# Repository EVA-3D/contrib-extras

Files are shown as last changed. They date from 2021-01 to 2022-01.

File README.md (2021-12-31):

# EVA-3D community contributions
This is the place that houses the community contributions that do not necessarily conform 100% to the standard EVA defines, but may still be useful in specific applications. This is also a place to share other things like spool holders, test prints, etc. If you have a part or a mod you want to list here, fork this repository, add your files, and [submit a pull request](https://github.com/EVA-3D/contrib-extras/pulls). Anyone is welcome to contribute, in fact, the more the merrier!

# How to contribute
Fork this repository and add your stls, an image preview and a page file for presenting your part.

Part descriptions are written in markdown (.md) files.

* The main page for your part should be in `docs/[category]/[your_part_name].md`
* Any assets linked from that page (images, etc) should be in `docs/[category]/assets`. All files should be prefixed with your part name.
* The STL(s) should be in `docs/[category]/stl`. All files should be prefixed with your part name.
* Take a look at [Pawel's Spool Holder](https://github.com/EVA-3D/contrib-extras/tree/main/docs/spool_holders) for inspiration.

If you're not familiar with Git, reach out to `@miklschmidt#2036` on discord, or get help on [the unofficial Rat Rig discord server](https://discord.gg/D62e8XNeYa).

Please note that all contributes are automatically subject to the terms of the [CC BY-SA 4.0 license](https://creativecommons.org/licenses/by-sa/4.0/).

Please! Share your candy!

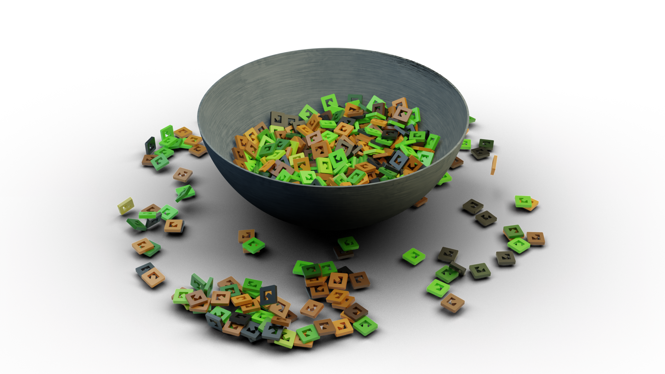
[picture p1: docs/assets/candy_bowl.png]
candy


## Local deployment 

There are two options, either you have a local Python envorinment with `Python` and `Poetry` or you can use Docker - the latter is easier but will be troublesome on Windows (since Windows is troublesome).

To get Docker go to https://docs.docker.com/get-docker/ and proceed with the installation steps. Do not be affraid in case you see this as black magic, Docker is a tool that allowes to run a tiny version of a Linux system on Mac, Windows and Linux - that tindy system is isolated from your machine - it's like a sandbox for developers.

> Per the documentation:
> It remains free for small businesses (fewer than 250 employees AND less than $10 million in annual revenue), **personal use**, education, and **non-commercial open source projects**.

Once it's installed you can use Docker Compose to deploy your own private EVA contrib site that will be visible only to you, go ahead and experiment with it to make sure your changes work before making a pull request :)

```
docker-compose up
```

And your local site will be accessible on the 127.0.0.1 address with is the loopback address pointing to your own machine: http://127.0.0.1:62999 is the full address and port.

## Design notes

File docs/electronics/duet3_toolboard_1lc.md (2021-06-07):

---
title: WichuR's Toolboard 1LC Horizontal Mount
---

> Created by: [Maciej Raczyński](https://github.com/wichur)

Allows mounting a Duet Toolboard 1LC v1.1 to the back plate in horizontal position. Alligned to keep within side boundaries of duct horns.

## Features
 - Positioned horizontally, above print fan
 - Vertical post for cable strain relief
 - Zip tie holes (2.5mm) for cable management
 - Place to support PTFE tube that helps to guide cables

## Compatibility
 - EVA 2.2.0 
 - Duet Toolboard 1LC v1.1
 - duet3_toolboard_1lc_common_support *Should* work also for v1.0

## Related EVA Parts
 - Replaces cable fin

## Assembly
 - Attaching Driver0 and IO connectors requires to temporarily unscrew toolboard
 - Use shorter screws to attach board to support
 - Use longer screws to attach lid

| No | Qty | Name | Printable |
| -- | --- | --- | --- |
| 1  | 2 | M3 x 8 mm | No |
| 2  | 2 | M3 x 18 mm | No |
| 3  | 4 | M3 Hex nuts | No |
| 3  | 10  | >2.5mm zip ties (optional) | No |
| 8  | 1 | Common Board Support | [Yes](stl/duet3_toolboard_1lc_common_support.stl) |
| 9  | 1 | Lid for Toolboard 1LC v 1.1(optional) | [Yes](stl/duet3_toolboard_1lc_v11_lid.stl) |

### How to attach incoming cables (CAN, VIN, PTFE tube, nylon sleeve)
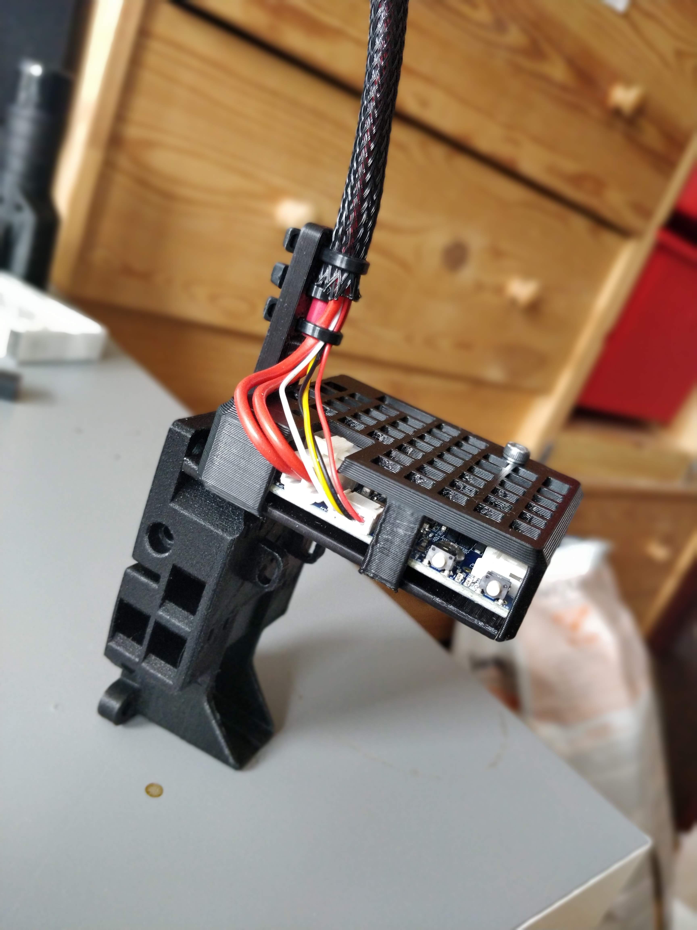
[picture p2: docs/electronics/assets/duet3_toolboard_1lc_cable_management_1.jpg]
cable management 1


### Sample cable management from appliances
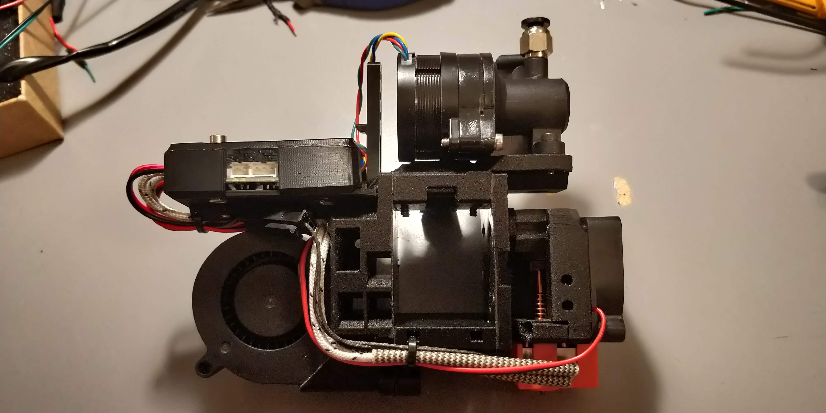
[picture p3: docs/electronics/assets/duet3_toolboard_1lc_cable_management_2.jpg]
cable management 2

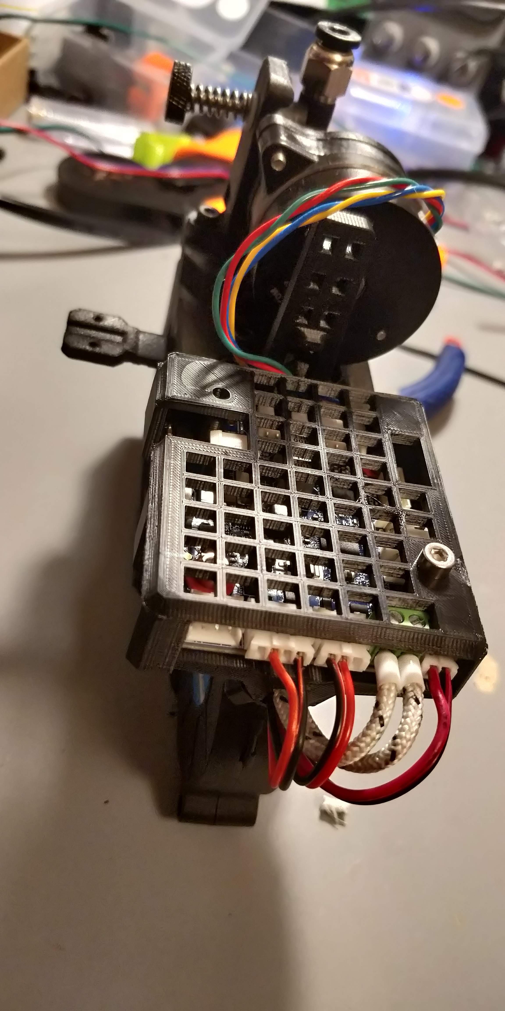
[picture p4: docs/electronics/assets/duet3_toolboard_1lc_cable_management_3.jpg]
cable management 3


### Print orientation
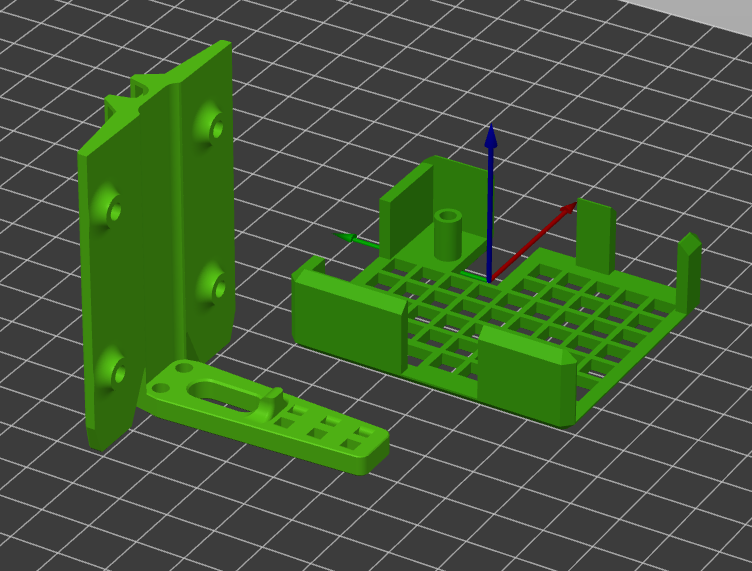
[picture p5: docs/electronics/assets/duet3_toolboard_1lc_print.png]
toolboard 1LC print orientation


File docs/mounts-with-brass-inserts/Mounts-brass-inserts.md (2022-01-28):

---
title: top_gun_de's Brass Inserts Remix
---

## Description:
> Created by: [Detlev Rackow](https://github.com/top-gun)

EVA is designed as a beginner-friendly carriage system, it is based on M3-screws and regular hex nuts. Brass inserts have several advantages over hex nuts: They won't fall out, and the risk of damage from too much torque is lower, especially in ABS and ASA parts. Inserting a brass inserts requires a soldering iron, and the inserts are a bit more expensive than the nuts.

EVA 2.4.1 was just released, and I modified relevant parts to accept brass inserts. The recommended sizes are M3x4.6x4 and M3x5x4. Don't use M3x5.6x4, as some holes are close to edges.

This repository contains 19 parts from EVA and two parts from the 5015 dual fan mod from Supersniffles.

I recommend to use these parts and complete your build with the parts from the regular EVA repository. The bottom part, for example, has no nut pockets so I did not modify it. The same is true for the probe mounts. You get these from the regular EVA 2.4-repository on github.

The "core" of EVA consists of:
- Universal face: Use from this contrib. Don't use the regular one, or support parts will get you into trouble.
- Top plate (holds the extruder): For Orbiter and Sherpa, use this contrib. For others use the regular parts.
- Bottom plate: Use from this contrib.
- Back plate (core-xy or cartesian): Use from this contrib.

To that, you attach a hotend face, most of these need a support part, too. Don't mix brass-fitted faces with regular support parts, they won't fit.

Fan ducts: These depend on the backplate. I clustered them into the carriage parts, together with the back plates.

Probe mounts: Use the regular ones. They have no nut pockets.

Shrouds: Use the regular parts. No nut pockets either.

## Compatible EVA versions

EVA 2.4.0 or later

## Carriage
### BOM - Carriage

| No | Qty | Name | Printable | Source
| -- | --- | --- | --- | ---
| 1  | 1 | Universal plate-brass | [Yes](stl/universal_face-2.4.1-inserts.stl) | [Onshape](https://cad.onshape.com/documents/74778ed34247d7556e100400/w/a58d330b6eac41d3ee1d6257/e/2d71e9f03f608830dc147b9e)
| 2  | 1 | backplate Core XY | [Yes](stl/back_corexy-2.4.1-inserts.stl) |  [Onshape](https://cad.onshape.com/documents/74778ed34247d7556e100400/w/a58d330b6eac41d3ee1d6257/e/5f6109f91396259629d149cf)
| 2a | 1 | backplate Cartesian | [Yes](stl/back_cartesian-2.4.1-inserts.stl) |  [Onshape](https://cad.onshape.com/documents/94ffc61ea8de2e8b4d175cb5/w/45370a8d35a588c223676b4b/e/29da292ee8a01c0ce953947a)
| 2b | 1 | backplate CoreXY-dual 5015 Supersniffles | [Yes](stl/dual_5015_back_v3_heat_inserts.stl) |  [Onshape](https://cad.onshape.com/documents/79d9ad219cc5cc9ce0dcf704/w/b53269836ac593db847c52c7/e/6edbe9540efb021b6a6e376c)
| 3  | 1 | Bottom plate MGN12 | [Yes](stl/bottom_mgn12_short_duct-inserts.stl) |  [Onshape](https://cad.onshape.com/documents/74778ed34247d7556e100400/w/a58d330b6eac41d3ee1d6257/e/884e27c8b1dbb4fb2e92761c)
| 3a | 1 | Bottom plate Dual 5015 MGN12 Supersniffles | [Yes](stl/dual_5015_bottom_v3.stl) |  [Onshape](https://cad.onshape.com/documents/9c252f9471d1d23ee56d6b70/w/959fe6d1b6f12c8dfe326720/e/2e778d9372bc94c95344f2a8)
| 4  | 1 | Tri-horn fan duct default | [Yes](stl/TriHorn-Duct-Default-2.4.2-inserts.stl) |  [Onshape](https://cad.onshape.com/documents/0032726621935a272d71ecdd/w/8c7ff9e179be83096c43302e/e/2895bb5dddef3b905fc26f3c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)
| 4a | 1 | Tri-horn fan duct default narrow | [Yes](stl/TriHorn-Duct-Default-Narrow-2.4.2-inserts.stl) |  [Onshape](https://cad.onshape.com/documents/0032726621935a272d71ecdd/w/8c7ff9e179be83096c43302e/e/2895bb5dddef3b905fc26f3c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)
| 4b | 1 | Tri-horn fan duct high | [Yes](stl/TriHorn-Duct-High-2.4.2-inserts.stl) |  [Onshape](https://cad.onshape.com/documents/0032726621935a272d71ecdd/w/8c7ff9e179be83096c43302e/e/2895bb5dddef3b905fc26f3c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)
| 4c | 1 | Tri-horn fan duct high narrow | [Yes](stl/TriHorn-Duct-High-Narrow-2.4.2-inserts.stl) |  [Onshape](https://cad.onshape.com/documents/0032726621935a272d71ecdd/w/8c7ff9e179be83096c43302e/e/2895bb5dddef3b905fc26f3c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)
| 4d | 1 | Tri-horn fan duct Volcano/Rapido UHF | [Yes](stl/TriHorn-Volcano-Duct-UHF-2.4.2-inserts.stl) |  [Onshape](https://cad.onshape.com/documents/0032726621935a272d71ecdd/w/8c7ff9e179be83096c43302e/e/2895bb5dddef3b905fc26f3c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)
| 4e | 1 | Dual 5015 Monster horn duct Supersniffles | [Yes](stl/dual_5015_monster_horns_duct_v2.3_heat_inserts.stl) |  [Onshape](https://cad.onshape.com/documents/9c252f9471d1d23ee56d6b70/w/959fe6d1b6f12c8dfe326720/e/18901272a3158b3c621a46d2)
| 4f | 1 | Dual 5015 Volcano/Rapido UHF duct (Tobi) | [Yes](stl/horn-rapido-uhf-2.4.1-inserts.stl) |  [Onshape](https://cad.onshape.com/documents/d0c8871ffd12a03b94cb6b30/w/60becf0a1f7f2dc8485e1bea/e/336a4f443bbbc477c9fbf4a0)
| 5  | 1 | Universal cable mount | [Yes](stl/unversal_cable_mount-2.4.2-inserts.stl) | [Onshape](https://cad.onshape.com/documents/74778ed34247d7556e100400/w/a58d330b6eac41d3ee1d6257/e/74e3872d67a8b60bdf4ad503)
| 6  | ##  | heat inserts brass M3 x D4.6 x L4 | No | [AliExpress](https://aliexpress.com/item/4000232858343.html)

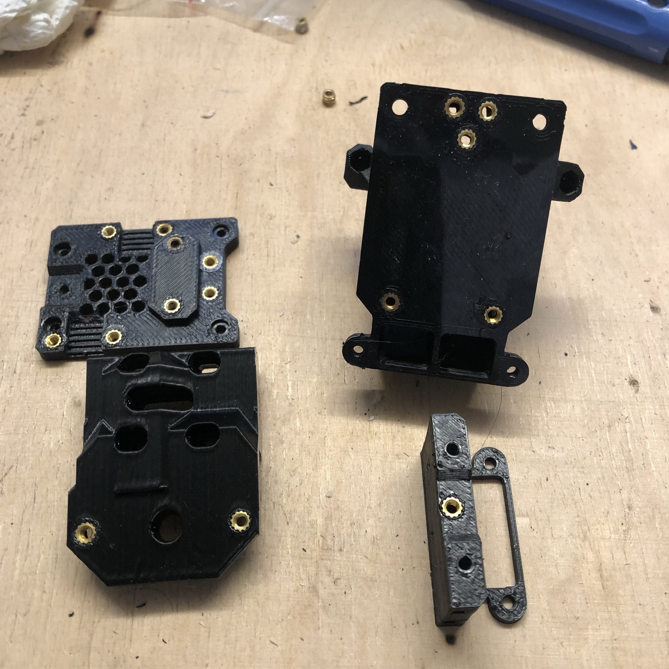
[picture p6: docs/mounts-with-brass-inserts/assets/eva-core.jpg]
Carriage


The picture are representative samples to show which holes get inserts.

A note on the Bondtech LGX lite extruder: It has integrated inserts, there are no hex nuts on the mounting plate. So just use the regular EVA 2.4.2 part.

## Extruders

### Orbiter 1.5, 2.0, Sherpa

[OnShape](https://cad.onshape.com/documents/081c89accea9ca68cd29ad9c/w/f873c4d34a84bfc1296409af/e/5655d7163b5af97b4bedc0b3)

| No | Qty | Name | Printable | Source
| -- | --- | --- | --- | ---
| 1a | 1 | Orbiter 1.5 top plate | [Yes](stl/top_orbiter_mgn12-2.4.1-inserts.stl) |
| 1b | 1 | Orbiter 2.0 top plate | [Yes](stl/top_orbiter_2_0_mgn12-2.4.1-inserts.stl) |
| 1c | 1 | Sherpa top plate | [Yes](stl/top_sherpa_mgn12-2.4.1-inserts.stl) |
| 2  | 2-3 | heat inserts brass M3 x D4.6 x L4 | No | [AliExpress](https://aliexpress.com/item/4000232858343.html)_

You find the Orbiter plate above in the picture of the carriage.

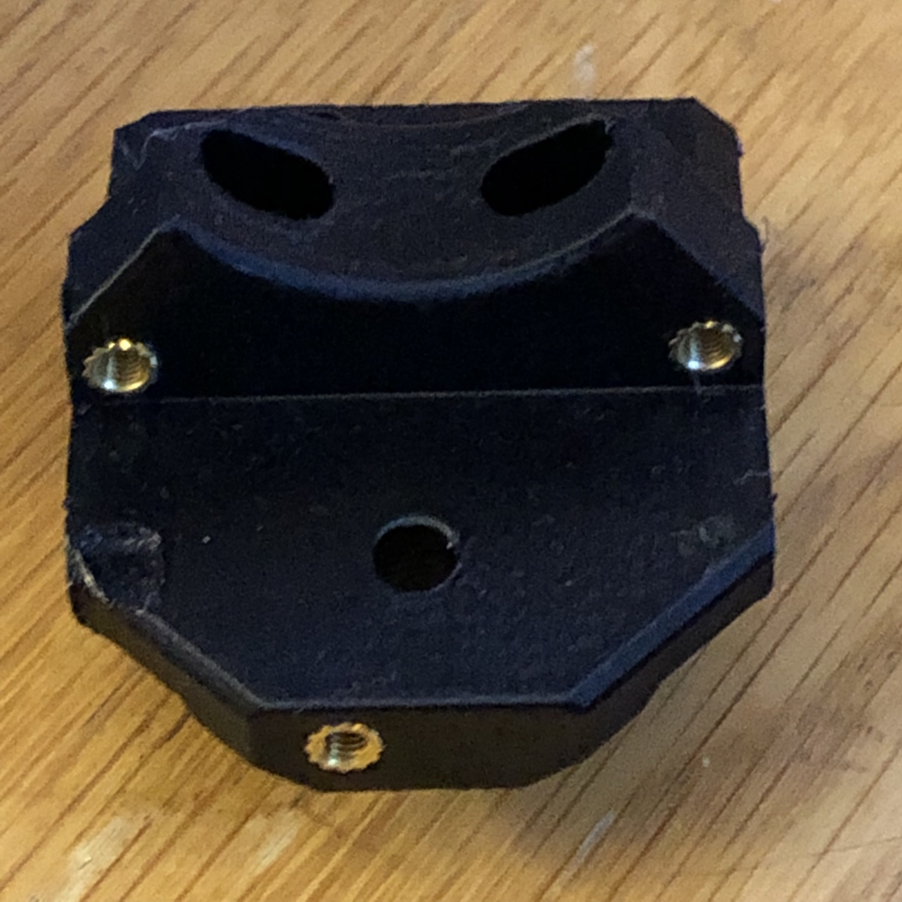
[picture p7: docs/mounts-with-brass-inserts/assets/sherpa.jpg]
Sherpa


## Hotends

### Mosquito

[OnShape](https://cad.onshape.com/documents/e2f2c2613337efae0a2ac6ae/w/d2d9cbef6cf272c261c0f9dd/e/01d1565488059980d5f63a9d)

| No | Qty | Name | Printable | Source
| -- | --- | --- | --- | ---
| 1  | 1 | Mosquito face | [Yes](stl/mosquito_face-2.4.2-insert.stl) |
| 2  | 1 | Mosquito support | [Yes](stl/mosquito_support-2.4.1-r2-insert.stl) |
| 3  | 6 | heat inserts brass M3 x D4.6 x L4 | No | [AliExpress](https://aliexpress.com/item/4000232858343.html)_

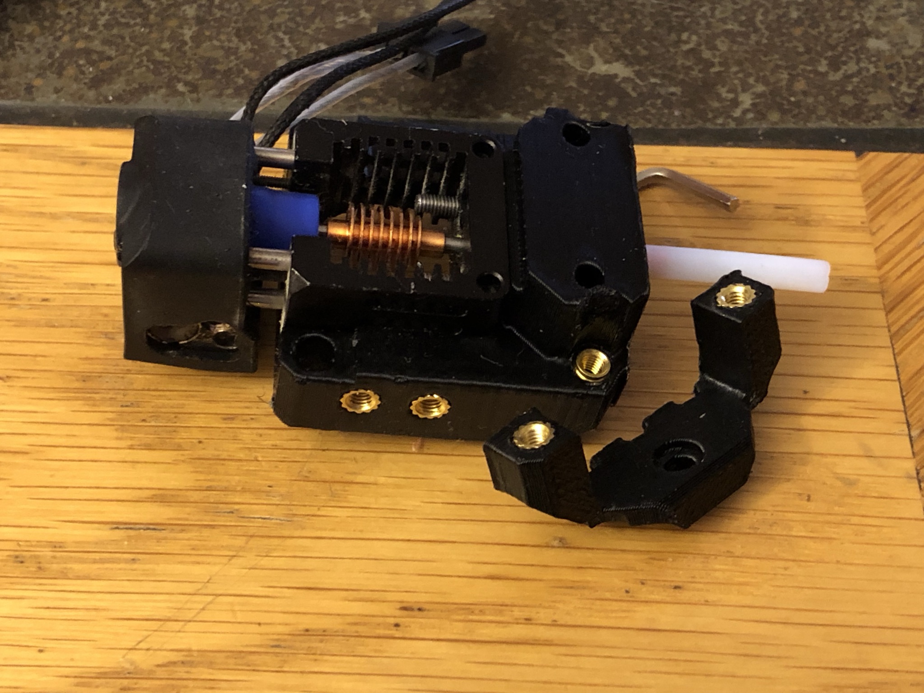
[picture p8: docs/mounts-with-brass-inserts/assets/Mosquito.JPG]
Mosquito


## Dragon
### BOM - Dragon

[OnShape](https://cad.onshape.com/documents/1ac22bf6c80ea191b6a184f7/w/7e460058ed8bcbd3f81da267/e/c3f35f6b538adc71dcb7ffb1)

| No | Qty | Name | Printable | Source
| -- | --- | --- | --- | ---
| 1  | 1 | Dragon face | [Yes](stl/dragon_face-2.4.2-inserts.stl) |
| 2  | 1 | Dragon support | [Yes](stl/v6_support-2.4.1-insert.stl) |
| 3  | 6 | heat inserts brass M3 x D4.6 x L4 | No | [AliExpress](https://aliexpress.com/item/4000232858343.html)_

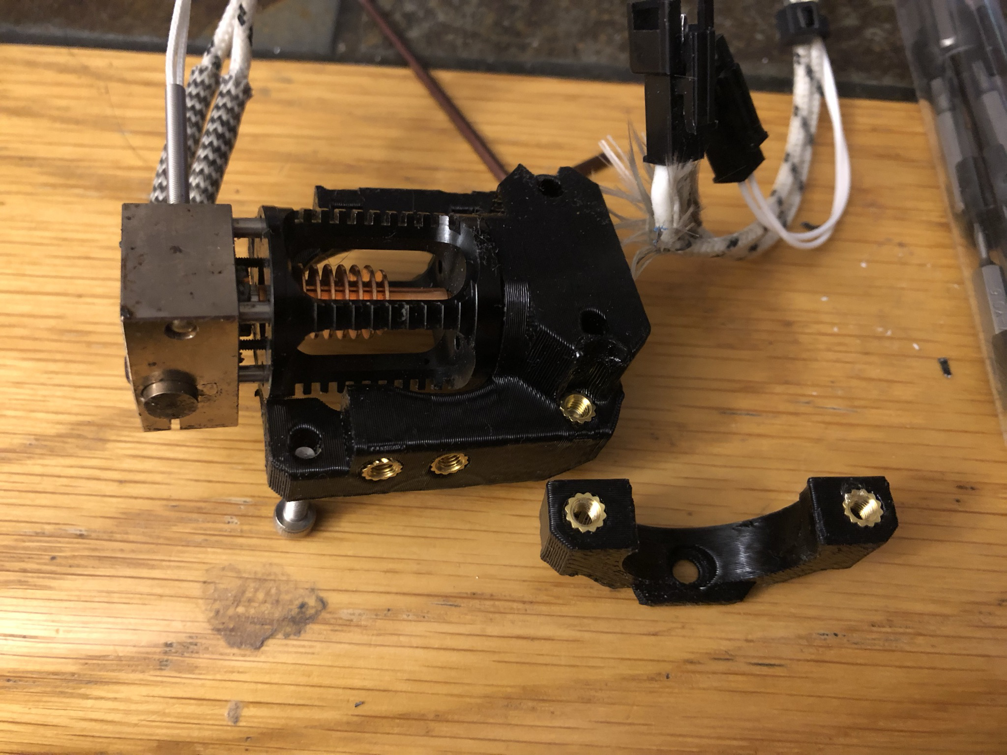
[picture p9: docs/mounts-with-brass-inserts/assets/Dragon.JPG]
Dragon


## Dragonfly BMO
### BOM - Dragonfly BMO

[OnShape](https://cad.onshape.com/documents/4c8353d7e6e4a8f4d1b76e65/w/0a82330b0b30b282d7d53988/e/12106137cd4e147d7a075002)

| No | Qty | Name | Printable | Source
| -- | --- | --- | --- | ---
| 1  | 1 | Dragonfly BMO face | [Yes](stl/bmo_face-2.4.1-inserts.stl) |
| 2  | 1 | Dragonfly BMO support | [Yes](stl/bmo_support-2.4.1-inserts.stl) |
| 3  | 6 | heat inserts brass M3 x D4.6 x L4 | No | [AliExpress](https://aliexpress.com/item/4000232858343.html)_

Sorry no picture, refer to the Dragon photo

### BOM - Rapido

[OnShape](https://cad.onshape.com/documents/2140634edd2879f7c6a038d7/w/9dabf35d413e6000239b7a0d/e/b796bd6e4476ec1504d2b277)

| No | Qty | Name | Printable | Source
| -- | --- | --- | --- | ---
| 1  | 1 | Rapido face (no support required) | [Yes](stl/face_rapido-2.4.1-inserts.stl) |
| 2  | 6 | heat inserts brass M3 x D4.6 x L4 | No | [AliExpress](https://aliexpress.com/item/4000232858343.html)_

Note: The Rapido in HF configuration (V6 nozzles) can use all regular fan ducts, i.e. Tri-horn-duct. For the UHF-configuration, use the longer Volcano/Rapido duct from Tobi (see above)

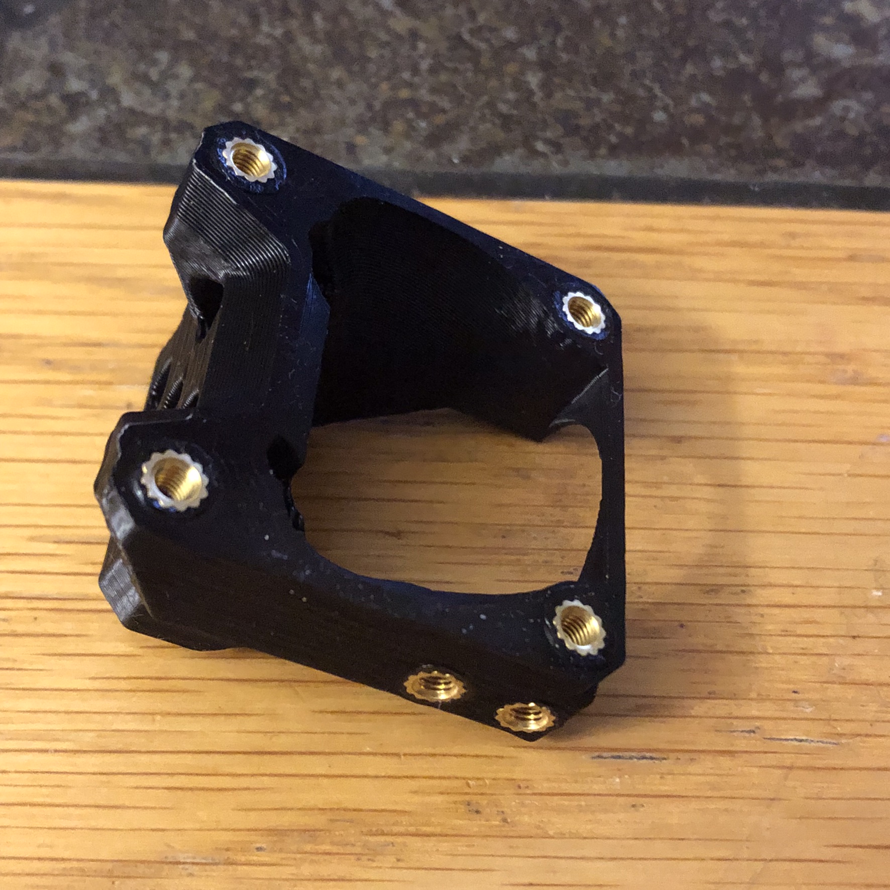
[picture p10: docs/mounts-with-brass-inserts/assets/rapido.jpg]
Rapido


### BOM - Nova

[OnShape](https://cad.onshape.com/documents/8bb78da485da9d371fa15665/w/dd52173389ed5d67ba8844b7/e/8d7a6916697bb187ac26cf42)

| No | Qty | Name | Printable | Source
| -- | --- | --- | --- | ---
| 1  | 1 | Nova face (no support required) | [Yes](stl/nova_face-2.4.1-inserts.stl) |
| 2  | 2 | heat inserts brass M3 x D4.6 x L4 | No | [AliExpress](https://aliexpress.com/item/4000232858343.html)_

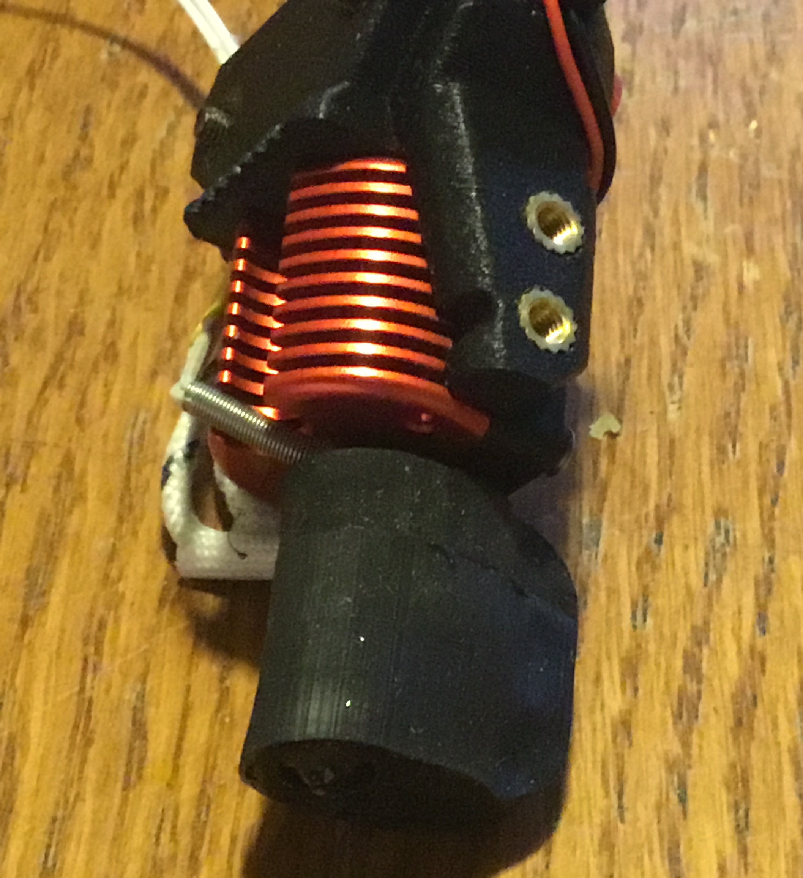
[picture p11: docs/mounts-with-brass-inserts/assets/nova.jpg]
Nova


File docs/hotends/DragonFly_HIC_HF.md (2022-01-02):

---
title: TheMacBoy's DragonFly HIC HF Hotend Mount
---

> Created by: [TheMacBoy](https://github.com/themacboy)

## Description
This is a [DragonFly HIC HF](https://www.phaetus.com/dragonfly-hf-hic) mount for the Phaetus hotend.

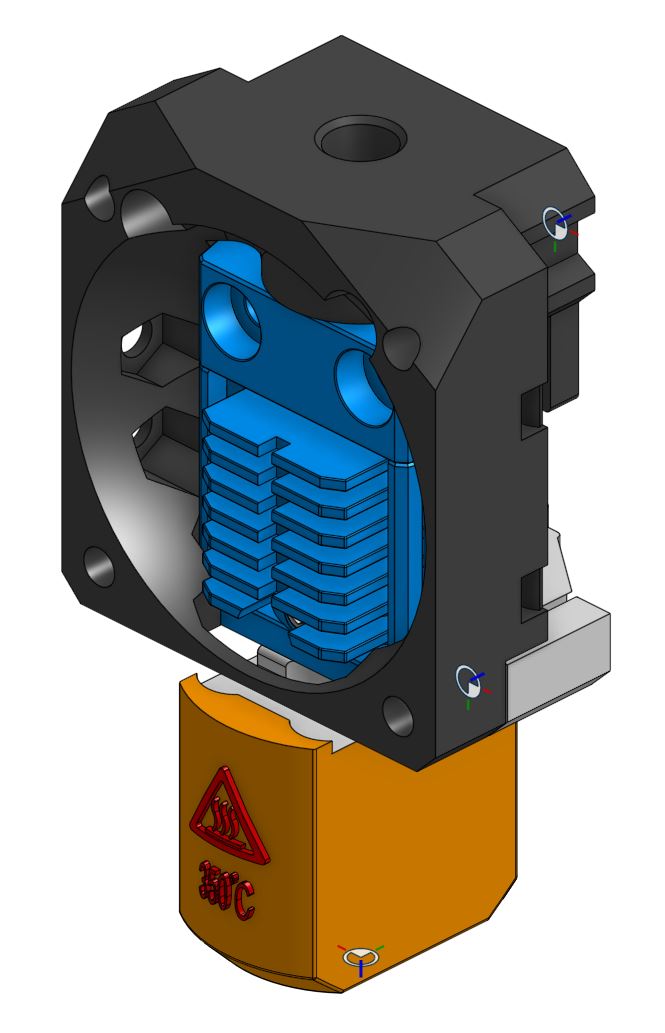
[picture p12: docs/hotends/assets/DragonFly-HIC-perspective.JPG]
DragonFly HIC HF


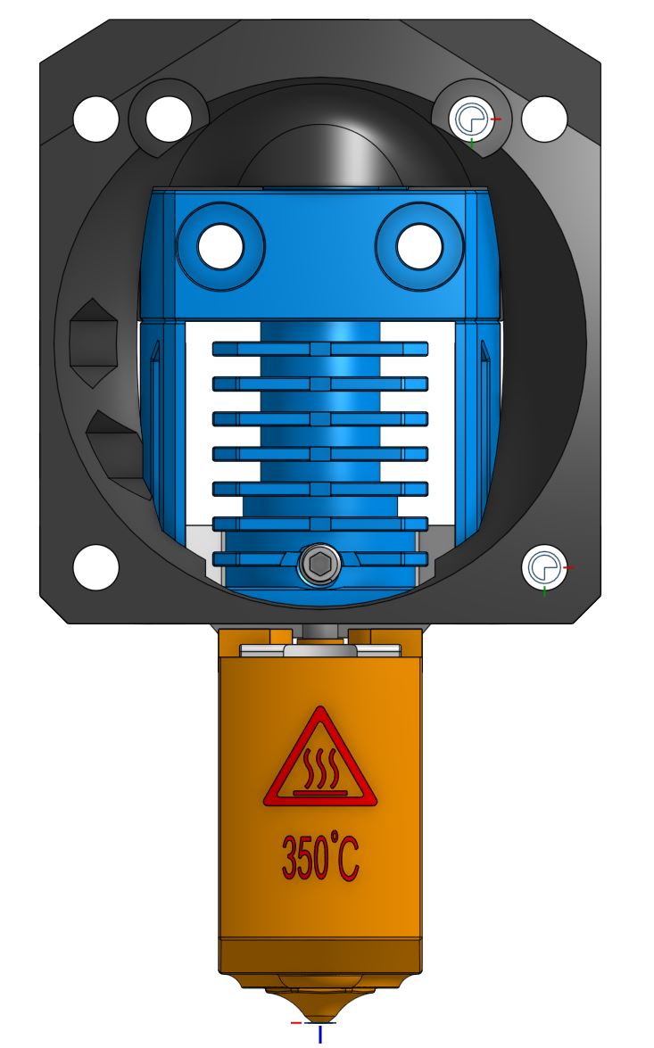
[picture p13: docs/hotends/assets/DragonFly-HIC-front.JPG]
DragonFly HIC front


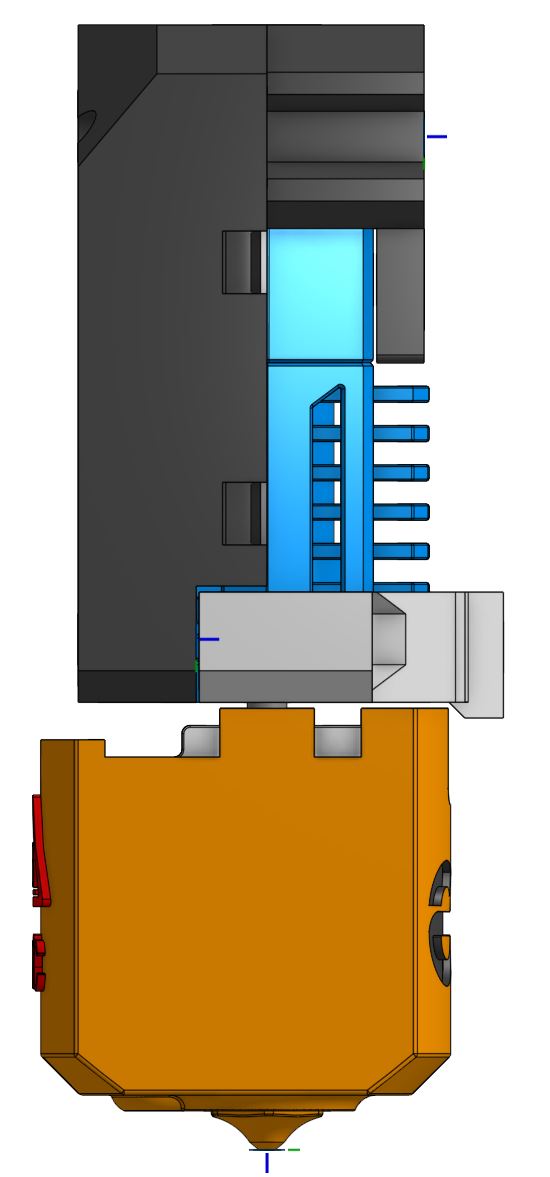
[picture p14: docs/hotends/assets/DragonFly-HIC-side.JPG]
DragonFly HIC side


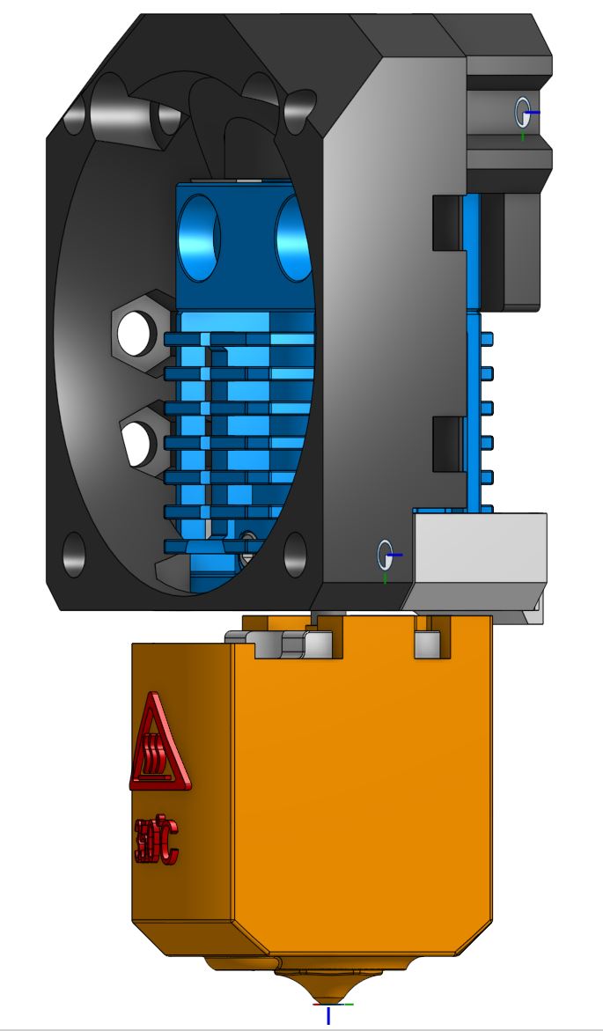
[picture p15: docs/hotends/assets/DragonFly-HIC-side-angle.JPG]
DragonFly HIC side_angle


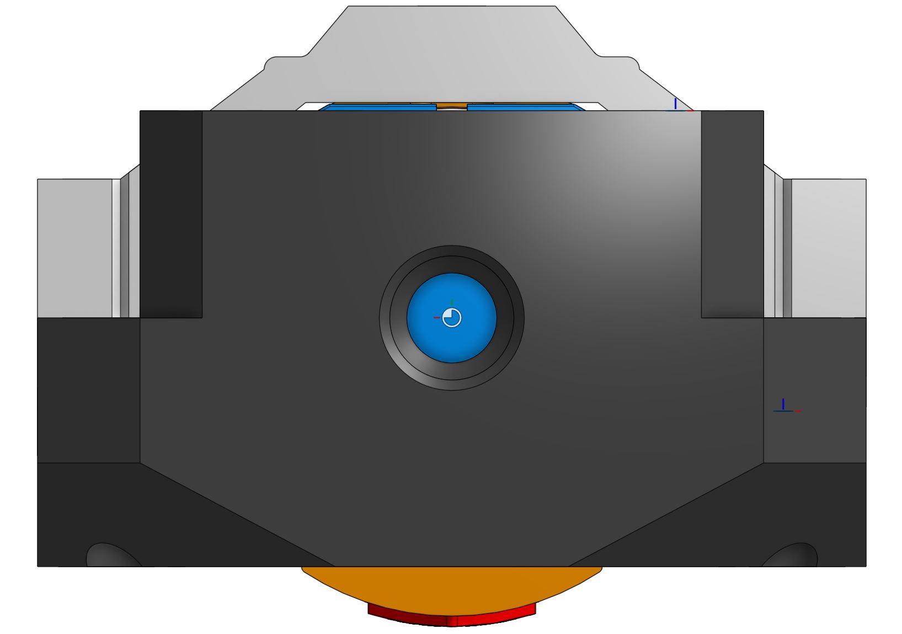
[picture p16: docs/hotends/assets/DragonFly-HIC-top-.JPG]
DragonFly HIC top


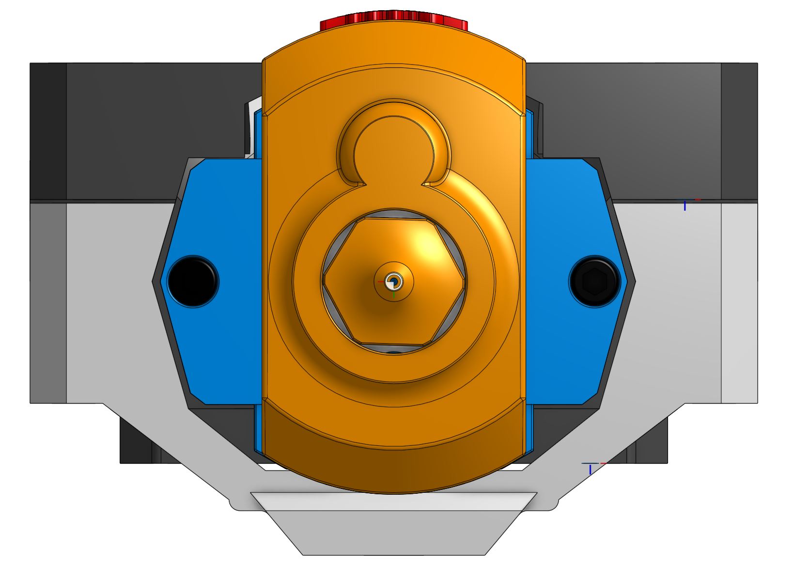
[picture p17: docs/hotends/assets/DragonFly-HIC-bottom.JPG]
DragonFly HIC bottom


## Compatible EVA version
2.2.0 - ?

## Related EVA parts
universal_face

## Source OnShape files
[DragonFly HIC HF](https://cad.onshape.com/documents/37f226ec31a6892e039799c4/w/9518350d2542991b8a0226ab/e/af757332e1b18b8f33156616)

## Changelog
v1.0 12/05/2021 TheMacBoy Release

## BOM:
| No | Qty | Name | Printable |
| -- | --- | --- | --- |
| 1  | 1 | [Face] eva-2.3-dragonfly-HIC-face.stl | [Yes](stl/eva-2.3-dragonfly-HIC-face.stl ) |
| 1  | 1 | [Support] eva-2.3-dragonfly-HIC-support.stl | [Yes](stl/eva-2.3-dragonfly-HIC-support.stl) |

## Hardware Required 
Standard EVA

## To Do 
Check if the hotend works at high speeds (+ 200 mm / s), I have currently removed some tolerances on the lower support to avoid vibrations.

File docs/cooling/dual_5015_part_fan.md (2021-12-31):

---
title: SuperSniffles' Dual 5015 Part Fan Mod
---

## Description

> Created by: Supersniffles (@SuperSniffles)

This Dual 5015 Part Fan mod replaces the single 5015 Part Fan located on the backplate with 2 5015 Part Fans. The mod is intended to supply a higher cooling capacity than the standard setup.

Version 2 of this mod is printable without support and doesn't require another MGN15 top. It also widens the bottom duct by 10mm and comes with a beefier horns duct to allow much more air to pass for better cooling performance. Version 2 supports both MGN15 and MGN12.

See [Dual 5015 Cable Chain](../cable_chain/dual_5015_part_fan_cable_chain.md) for cable chain support.

Note: Parts 4 and 8 are modified versions for use with brass heated inserts, modified by top_gun_de. They replace parts 3 and 7.

V2

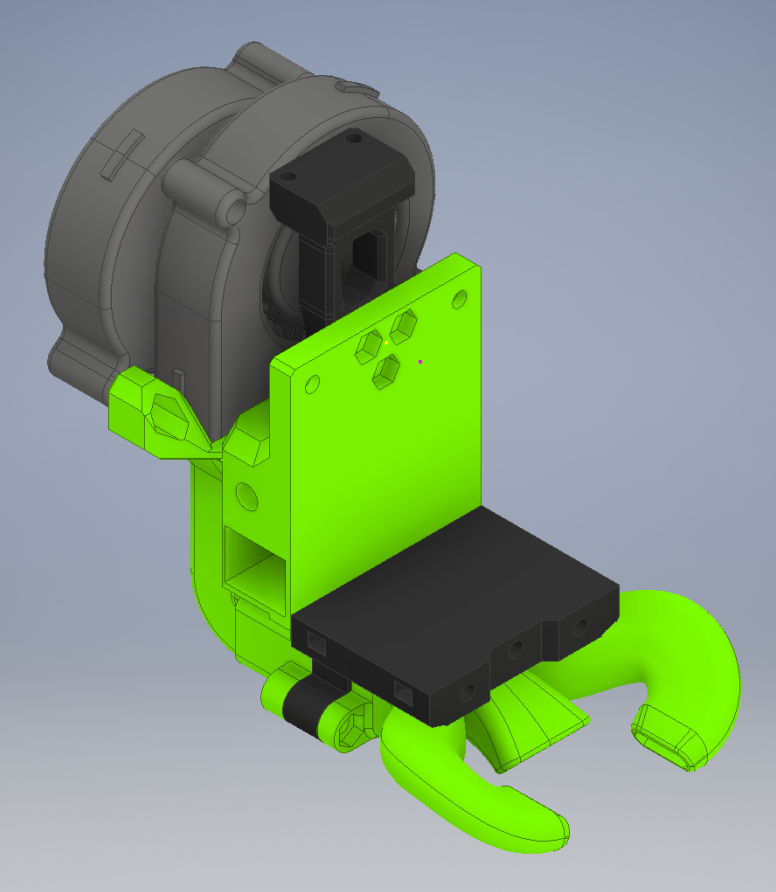
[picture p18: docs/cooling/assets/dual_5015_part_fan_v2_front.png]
Dual 5015 Part Fan Mod v2 front

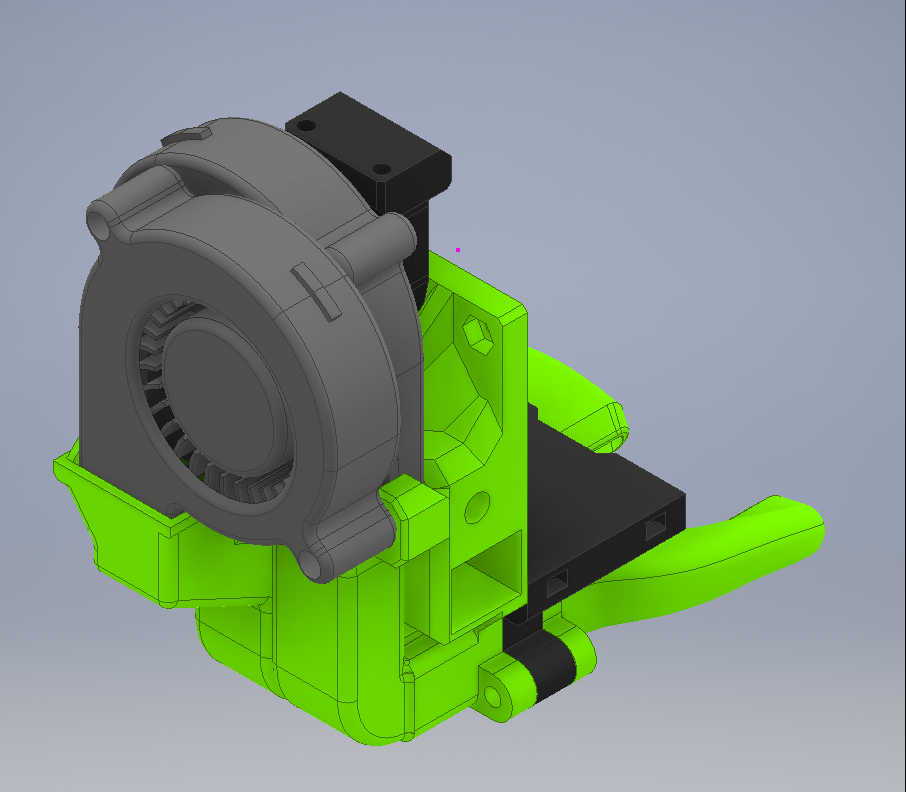
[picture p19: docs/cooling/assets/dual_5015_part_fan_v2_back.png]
Dual 5015 Part Fan Mod v2 back


V1

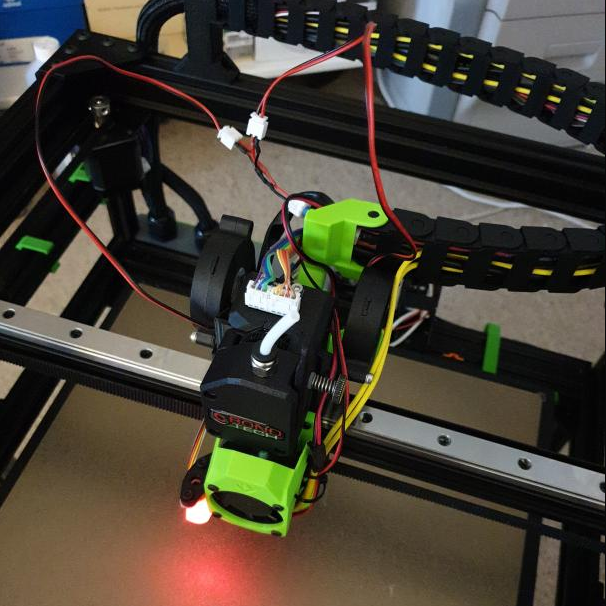
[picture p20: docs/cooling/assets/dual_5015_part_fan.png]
Dual 5015 Part Fan Mod v1


## Compatible EVA version
2.0.0 --> 2.4.1

## Related EVA Parts
This mod replaces `back_corexy` and `top_bmg_mgn15`

## V2 BOM
| No | Qty | Name | Printable |
| -- | --- | --- | --- |
| 1  | 2 | 5015 Blower Fan | No |
| 2  | ? | Various M3 screws | No |
| 3  | 1 | dual_5015_back_v2.0 | [Yes](stl/dual_5015_back_v2.0.stl) |
| 4  | 1 | dual_5015_back_v2.0_heat_inserts (Optional) | [Yes](stl/dual_5015_back_v2.0_heat_inserts.stl) |
| 5  | 1 | dual_5015_bottom_mgn12_wide | [Yes](stl/dual_5015_bottom_mgn12_wide.stl) |
| 6  | 1 | dual_5015_bottom_mgn15_wide | [Yes](stl/dual_5015_bottom_mgn15_wide.stl) |
| 7  | 1 | dual_5015_monster_horns_duct_v2.3 | [Yes](stl/dual_5015_monster_horns_duct_v2.3.stl) |
| 8  | 1 | dual_5015_monster_horns_duct_v2.3_inserts (Optional) | [Yes](stl/dual_5015_monster_horns_duct_v2.3_heat_inserts.stl) |
| 9  | 1 | dual_5015_adxl_mount_v2.0 | [Yes](stl/dual_5015_adxl_mount_v2.0.stl) |

## V1 BOM
| No | Qty | Name | Printable |
| -- | --- | --- | --- |
| 1  | 2 | 5015 Blower Fan | No |
| 2  | ? | Various M3 screws | No |
| 3  | 1 | dual_5015_part_fan_core_xy_back | [Yes](stl/dual_5015_part_fan_core_xy_back.stl) |
| 4  | 1 | dual_5015_part_fan_top_bmg_mgn15 | [Yes](stl/dual_5015_part_fan_top_bmg_mgn15.stl) |
| 5  | 1 | dual_5015_part_fan_connector | [Yes](stl/dual_5015_part_fan_connector.stl) |

## Print instructions
LH = 0.2

Nozzle = 0.4

Supports needed for V1, no supports needed for V2

## V2 Step Files
[Dual 5015 Part Fan Core XY Back V2](assets/dual_5015_back_v2.0.stp)

[Dual 5015 Part Fan MGN12 Wide Bottom](assets/dual_5015_bottom_mgn12_wide.stp)

[Dual 5015 Part Fan MGN15 Wide Bottom](assets/dual_5015_bottom_mgn15_wide.stp)

[Dual 5015 Part Fan Monster Horns Duct](assets/dual_5015_monster_horns_duct_v2.3.stp)

[Dual 5015 Part Fan ADXL Mount](assets/dual_5015_adxl_mount_v2.0.stp)

## V1 Step Files
[Dual 5015 Part Fan Core XY Back](assets/dual_5015_part_fan_core_xy_back.stp)

[Dual 5015 Part Fan Top BMG MGN15](assets/dual_5015_part_fan_top_bmg_mgn15.stp)

[Dual 5015 Part Fan Connector](assets/dual_5015_part_fan_connector.stp)

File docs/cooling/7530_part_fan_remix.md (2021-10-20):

---
title: Ed Boston's 7530 Part Fan Mod Remix
---

## Description

> Created by: [Ed Boston](https://github.com/eboston)

This is a remix of the 7530 Part Fan Mod by [Mikkel Schmidt](7530_part_fan.md) with two changes.
  1) Added a second mounting point for the fan
  2) Added a slot for inserting the nuts at the bottom.

I was unable to get the nuts into their location and seated.  I added a slot so the nut can be dropped in easily.

Additional files can be found in [Mikkel Schmidt](7530_part_fan.md) mod.

From [Mikkel Schmidt](7530_part_fan.md):
This mod replaces the Core XY back with a 7530 fan mount to provide additional cooling capacity over the stock 5015. It uses a wider MGN bottom and monster duct from version 2 of [SuperSniffles' Dual 5015 Mod](dual_5015_part_fan.md).
Only supports MGN12 at this time, but is compatible with supersniffles' mgn12_wide bottom, only the split in the middle might decrease performance a tiny bit. Your mileage may vary.

Alternatively you can use the Occam's duct that i made, which also seem to perform very well, especially for low pressure fans. An extra benefit is that it's much less prone to warping at higher temperatures. In fact i've been using a PLA version without issues at 90 degrees bed temperature.

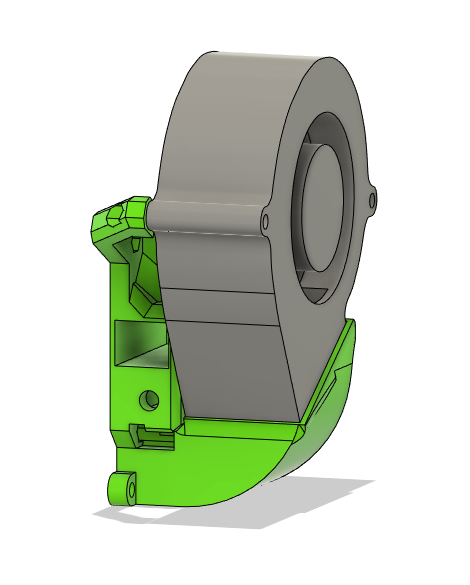
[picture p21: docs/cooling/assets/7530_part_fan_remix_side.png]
7530 Fan Remix

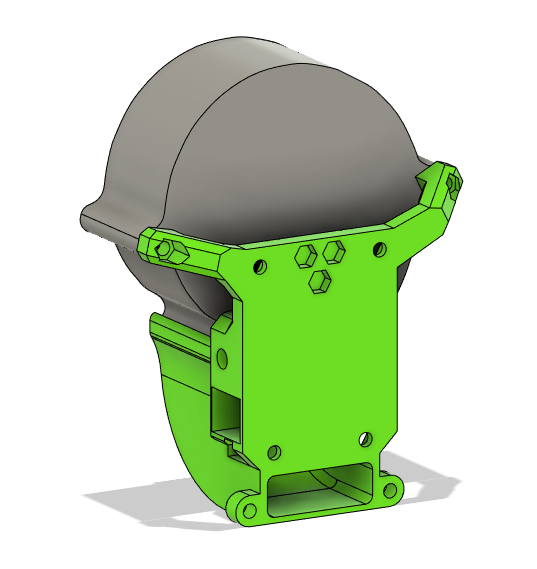
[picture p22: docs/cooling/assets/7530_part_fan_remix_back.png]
7530 Fan Mod


## Compatible EVA version
2.0 and newer.

## BOM
| No | Qty | Name | Printable |
| -- | --- | --- | --- |
| 1  | 2 | M3 hex nut | No |
| 2  | 2 | M3 x 40mm | No |
| 3  | 1 | 7530 EVA Back | [Yes](stl/7530_part_fan_remix.stl) |

## Print instructions
Follow the general EVA guidelines. At least 2 perimeters and 20% infill at .2mm or .3mm layer height. No supports needed.

## Step files
[7530 Back](assets/7530_part_fan_remix.step)

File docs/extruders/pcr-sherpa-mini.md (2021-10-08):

---
title: P-C-R's Sherpa Mini Mount
---

> Created by: P-C-R

## Description
This is a replacement top plate to support the Annex Engineering Sherpa Mini RC1 extruder

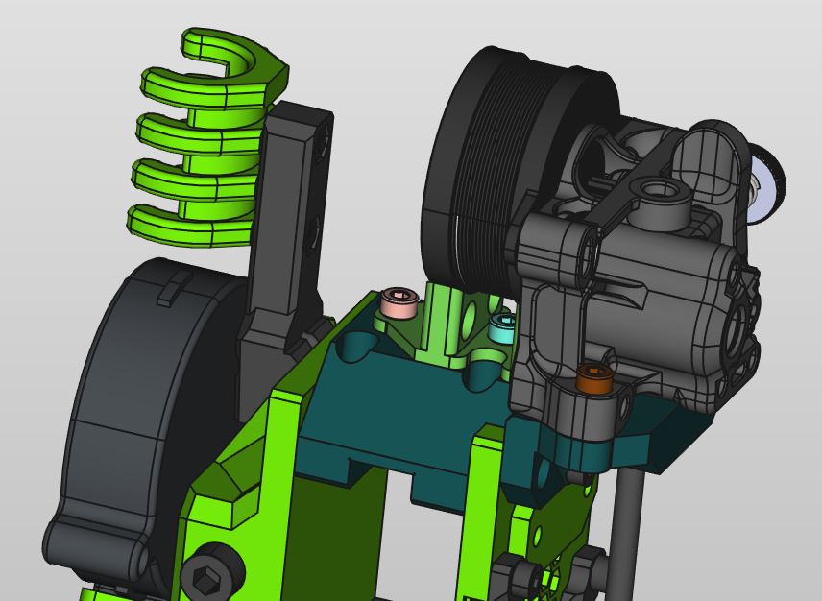
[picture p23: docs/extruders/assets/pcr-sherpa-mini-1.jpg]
pcr-sherpa-mini-1

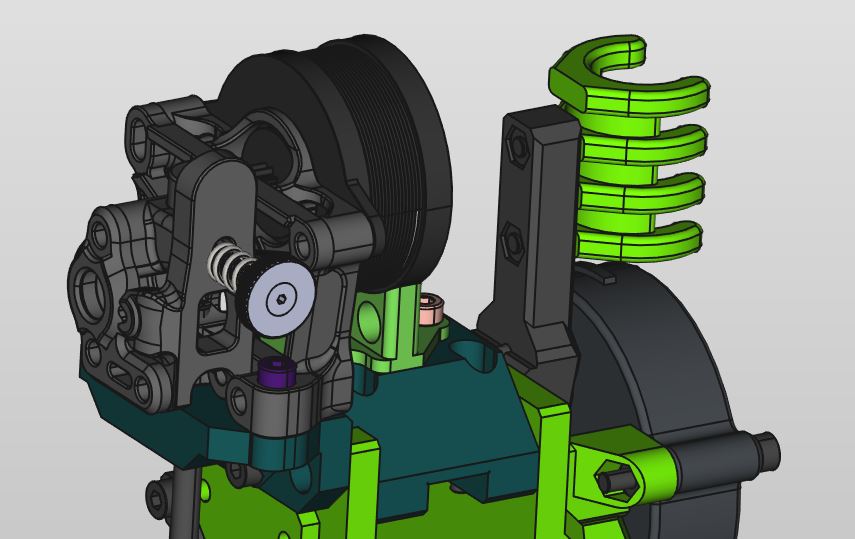
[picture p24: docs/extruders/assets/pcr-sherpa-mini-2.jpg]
pcr-sherpa-mini-2

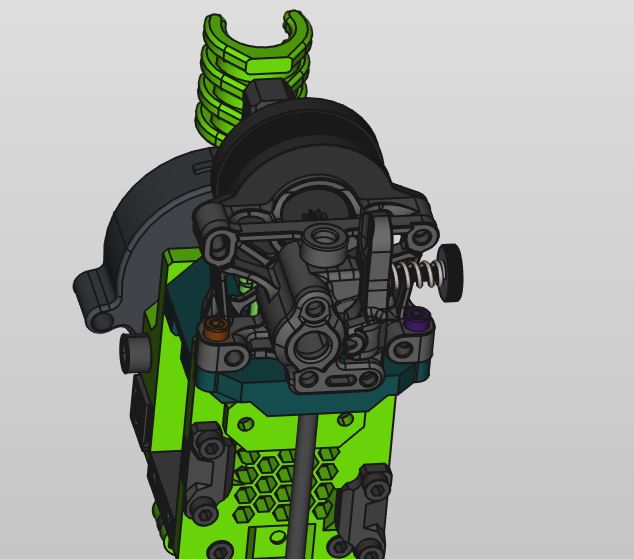
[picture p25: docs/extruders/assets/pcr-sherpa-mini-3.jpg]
pcr-sherpa-mini-3


## Compatible EVA version
2.4.0 (unreleased, get the universal plate from the EVA Onshape document)

## Printing instructions
You have to print the main mount upside down with supports for the slot holes

## BOM
| No  | Qty | Name | Printable |
| --- | --- | --- | --- |
| 1 | 2 | M3x12 | No |
| 2 | 2 | M3x6 | No |
| 3 | 2 | M3x5 Heated insert | No |
| 4 | 2 | M3x12 | No |
| 5 | 1 | pcr-sherpa-mini-main-mount | [Yes](stls/pcr-sherpa-mini-main-mount.stl) |
| 6 | 1 | pcr-sherpa-mini-motor-holder | [Yes](stls/pcr-sherpa-mini-motor-holder.stl) |

## .STEP files

[pcr-sherpa-mini-main-mount.step](assets/pcr-sherpa-mini-main-mount.step)

[pcr-sherpa-mini-motor-holder.step](assets/pcr-sherpa-mini-motor-holder.step)

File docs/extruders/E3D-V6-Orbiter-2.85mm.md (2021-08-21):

---
title: Ruffle's E3D V6 & Orbiter 2.85mm Mod
---

## Description

> Created by: Ruffle

This is a modified EVA 2.4 top plate for the Orbiter F2.85 and an E3D V6 2.85mm Bowden Heatsink.

It will only work with the EVA 2.4 Universal front plate, or possibly later, as the notch is a different size to earlier versions and V2.4 added the additional screws to sandwich the the Universal front plate.

You will need two M3x8 Button Head screws - normal socket head's won't fit as the top of the heatsink will hit them and two M3 heatset inserts for the Orbiter mounting screws. I used Ruthex M3x5.7 for a bit more plastic engagement.

The PTFE tube (6.35mm OD) should, in theory, be 37mm long if you can get it all the way into the E3D Heatsink. Possibly more useful is that it should protrude 9mm from the top of the mounting plate to correctly locate in the Orbiter F2.85 body.

Note:  The F2.85 Orbiter has a different footprint to the V1.5.  Dr Robert Lorincz says that the V2 Orbiter for 1.75mm filament, due Aug '21, will have the same footprint as this F2.85 version.

E3D V6 Orbiter 2.85mm
E3D V6 Orbiter 2.85mm on Mount
E3D V6 Orbiter 2.85mm Sub Assembly

## Compatible EVA version
2.4

## Related EVA Parts
This mod replaces `top_orbiter_mgn12`

## BOM
| No  | Qty | Name | Printable |
| --- | --- | --- | --- |
| 1 | 2 | DIN 7380 M3x8 Button Head screws | No |
| 2 | 2 | Ruthex RX-M3x5.7 Heatset Inserts | No |
| 3 | 1 | E3D V6 Orbiter 2.85mm Top | [Yes](stls/E3D-V6-Orbiter-2.85mm.stl) |

## Print instructions
LH = 0.2

Nozzle = 0.4

## Step Files
[E3D V6 Orbiter 2.85mm Top](assets/E3D-V6-Orbiter-2.85mm.stp)

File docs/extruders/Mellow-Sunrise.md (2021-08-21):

---
title: Mellow Sunrise mount (Volcano + Normal)
---

> Created by: [dmason1992](https://github.com/dmason1992)

## Description
This is a replacement front plate for mounting the Mellow Sunrise extruder/hotend combo. Note all standard ducts will need extending to reach the nozzle.

[Mellow Sunrise STEP file](stls/Mellow-Sunrise.step)

Mellow Sunrise

[Mellow Sunrise Volcano STEP file](stls/Mellow-Sunrise-Volcano.step)

Mellow Sunrise

[Mellow Sunrise Volcano with SuperSniffels dual 5015 fan mod STEP file](stls/Mellow-Sunrise-Volcano-Dual5015-Monsterduct.step)

Mellow Sunrise

## Compatible EVA version
2.3.0

## Related EVA parts
Height of nozzle on both normal and volcano versions allow use of all the standard ducts. However they need extended or and extender added along with 20mm longer bolts.

## Changelog
v1.0 04/08/2021 - Initial Release

V1.1 09/08/2021 - Added files for monster duct + dual5015 compatibility

v1.2 12/08/2021 - modified standard + volcano single 5015 fan versions to have the extended duct portion on the bottom part so that standard ducts can be used.

## BOM (Standard):
| No  | Qty | Name | Printable |
| --- | --- | --- | --- |
| 1 | 1 | Mellow-Sunrise-Front-Plate.stl | [Yes](stls/Mellow-Sunrise-Front-Plate.stl) |
| 1 | 1 | Mellow-Sunrise-Universal-Probe-Mount-Adapter.stl | [Yes](stls/Mellow-Sunrise-Universal-Probe-Mount-Adapter.stl) |

## BOM (Volcano):
| No  | Qty | Name | Printable |
| --- | --- | --- | --- |
| 1 | 1 | Mellow-Sunrise-Front-Plate-Volcano.stl | [Yes](stls/Mellow-Sunrise-Front-Plate-Volcano.stl) |
| 1 | 1 | Mellow-Sunrise-Universal-Probe-Mount-Adapter-Volcano.stl | [Yes](stls/Mellow-Sunrise-Universal-Probe-Mount-Adapter-Volcano.stl) |

## BOM (Volcano - wide duct):
Take the duct + back plate from supersniffles mod folder

| No  | Qty | Name | Printable |
| --- | --- | --- | --- |
| 1 | 1 | Mellow-Sunrise-Front-Plate-Volcano.stl | [Yes](stls/Mellow-Sunrise-Front-Plate-Volcano.stl) |
| 1 | 1 | Mellow-Sunrise-Universal-Probe-Mount-Adapter-Volcano.stl | [Yes](stls/Mellow-Sunrise-Universal-Probe-Mount-Adapter-Volcano.stl) |
| 1 | 1 | Mellow-Sunrise-Bottom-Wide-Duct-Extended.stl | [Yes](stls/Mellow-Sunrise-Bottom-Wide-Duct-Extended.stl) |

## Hardware Required 
Standard EVA

## To Do 
Physically test assembly, fit and performance. See if it performs better than the other heavier front heavy EVA's

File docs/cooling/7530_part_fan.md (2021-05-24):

---
title: Mikkel Schmidt's 7530 Part Fan Mod
---

## Description

> Created by: [Mikkel Schmidt](https://github.com/miklschmidt)

This mod replaces the Core XY back with a 7530 fan mount to provide additional cooling capacity over the stock 5015. It uses a wider MGN bottom and monster duct from version 2 of [SuperSniffles' Dual 5015 Mod](dual_5015_part_fan.md).
Only supports MGN12 at this time, but is compatible with supersniffles' mgn12_wide bottom, only the split in the middle might decrease performance a tiny bit. Your mileage may vary.

Alternatively you can use the Occam's duct that i made, which also seem to perform very well, especially for low pressure fans. An extra benefit is that it's much less prone to warping at higher temperatures. In fact i've been using a PLA version without issues at 90 degrees bed temperature.

7530 Fan Mod
7530 Fan Mod

## Compatible EVA version
2.0 and newer.

## BOM
| No | Qty | Name | Printable |
| -- | --- | --- | --- |
| 1  | 1 | M3 hex nut | No |
| 1  | 1 | M3 x 35mm | No |
| 6  | 1 | 7530 EVA Back | [Yes](stl/7530_fan_back_corexy.stl) |
| 6  | 1 | 7530 MGN12 Bottom Wide | [Yes](stl/7530_fan_mgn12_bottom_wide.stl) |
| 6  | 1 | SuperSniffles' Monster Duct v2.3 | [Yes](stl/dual_5015_monster_horns_duct_v2.3.stl) |
| 6  | 1 | Occam's Duct | [Yes](stl/7530_fan_occams_duct.stl) |

## Print instructions
Follow the general EVA guidelines. At least 2 perimeters and 20% infill at .2mm or .3mm layer height. No supports needed.

## Step files
[7530 Back](assets/7530_back_corexy.step)

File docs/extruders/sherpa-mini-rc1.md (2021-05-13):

---
title: Boont's Sherpa Mini RC1 Mount
---

> Created by: [Boont](https://github.com/silvalis)

## Description
This is a replacement top plate to support the Annex Engineering Sherpa Mini RC1 extruder

sherpa-mini-rc1

## Compatible EVA version
2.1.0 - 2.2.1

## Related EVA parts

## Changelog
v1.0 31/03/2021 Boont Release

## BOM:
| No | Qty | Name | Printable |
| -- | --- | --- | --- |
| 1  | 1 | sherpa-mini-eva2-mgn12.stl | [Yes](stls/sherpa-mini-eva2-mgn12.stl) |
| 1  | 1 | sherpa-mini-eva2-mgn15c.stl | [Yes](stls/sherpa-mini-eva2-mgn15c.stl) |

## Additional files required

## Hardware Required 
Standard EVA

## To Do

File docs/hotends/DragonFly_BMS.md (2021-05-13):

---
title: TheMacBoy's DragonFly BMS Hotend Mount
---

> Created by: [TheMacBoy](https://github.com/themacboy)

## Description
This is a DragonFly BMS mount for the Phaetus hotend.

DragonFly BMS front

DragonFly BMS rear

DragonFly BMS bottom

## Compatible EVA version
2.2.0 - ?

## Related EVA parts
universal_face

## Source OnShape files
[DragonFly BMS](https://cad.onshape.com/documents/f5b4dc864f32153dba7690b3/w/8f750729d643301faf8fc3c8/e/c2ebd73578bb9fa59d6904bc)

## Changelog
v1.0 12/05/2021 TheMacBoy Release

## BOM:
| No | Qty | Name | Printable |
| -- | --- | --- | --- |
| 1  | 1 | [Face] eva-2.2-dragonfly-bms-face.stl | [Yes](stl/eva-2.2-dragonfly-bms-face.stl) |
| 1  | 1 | [Face] eva-2.2-dragonfly-bms-support.stl | [Yes](stl/eva-2.2-dragonfly-bms-support.stl) |

## Hardware Required 
Standard EVA

## To Do

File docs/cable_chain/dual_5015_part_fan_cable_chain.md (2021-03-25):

---
title: SuperSniffles' Cable Chain Mount for Dual 5015 Mod
---

## Description

> Created by: Supersniffles (@SuperSniffles)

This addon to the [Dual 5015 Part Fan Mod](../cooling/dual_5015_part_fan.md) adds 10x20 cable chain support by replacing the Universal Cable Mount for the EVA Back.

Dual 5015 Part Fan Mod

## Compatible EVA version
2.0.0 --> 2.2.1

## Related EVA Parts
This mod replaces the universal cable mount.

## BOM
| No | Qty | Name | Printable |
| -- | --- | --- | --- |
| 1  | 3 | M3 x 10mm | No |
| 1  | 3 | M3 nuts | No |
| 6  | 1 | dual_5015_part_fan_cable_chain | [Yes](stl/dual_5015_part_fan_cable_chain.stl) |
| 6  | 1 | dual_5015_part_fan_cable_chain_frame | [Yes](stl/dual_5015_part_fan_cable_chain_frame.stl) |

## Print instructions
LH = 0.2

Nozzle = 0.4

Supports needed

## Step Files
[Dual 5015 Part Fan Core XY Back](assets/dual_5015_part_fan_cable_chain.stp)

[Dual 5015 Part Fan Top BMG MGN15](assets/dual_5015_part_fan_cable_chain_frame.stp)

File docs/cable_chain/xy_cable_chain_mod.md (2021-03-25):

---
title: SuperSniffles' XY Cable Chain Mod
---

## Description

> Created by: Supersniffles (@SuperSniffles)

This Mod adds XY cable chain support to the V-Core Pro.
Use `xy_cable_chain_extruder_mount_std` for the original setup with one fan on the back, and `xy_cable_chain_extruder_mount` if you already use my 5015 dual fan mod.

Dual 5015 Part Fan Mod

## Compatible EVA version
2.0.0 --> 2.2.1

## Related EVA Parts
This mod has only been tested with a BMG setup, but should work with all top mounted extruders.

The `xy_cable_chain_back_adxl_opt` is for mounting an ADXL in place of the Universal Cable Mount.

The `xy_cable_chain_stepper_slider` is mounted to the two holes on the top of the extruder mount, and prevents the X chain from getting caught on the carriage.

The `xy_cable_chain_extruder_mount(_std)` mounts to the bottom hole in the side of the extruder mount and one hole of the MGN top.

## BOM
| No | Qty | Name | Printable |
| -- | --- | --- | --- |
| 1  | ? | M3 screws | No |
| 2  | ? | M3 nuts | No |
| 3  | 2 | Cable Chain | [Amazon](https://www.amazon.de/gp/product/B07VGC8QJR/) |
| 4  | 1 | xy_cable_chain_back_adxl_opt | [Yes](stl/xy_cable_chain_back_adxl_opt.stl) |
| 5  | 1 | xy_cable_chain_extruder_mount_std | [Yes](stl/xy_cable_chain_extruder_mount_std.stl) |
| 6  | 1 | xy_cable_chain_extruder_mount | [Yes](stl/xy_cable_chain_extruder_mount.stl) |
| 7  | 1 | xy_cable_chain_xy_joiner_hood | [Yes](stl/xy_cable_chain_xy_joiner_hood.stl) |
| 8  | 1 | xy_cable_chain_xy_joiner | [Yes](stl/xy_cable_chain_xy_joiner.stl) |
| 9  | 1 | xy_cable_chain_stepper_slider | [Yes](stl/xy_cable_chain_stepper_slider.stl) |

## Print instructions
LH = 0.2

Nozzle = 0.4

Supports needed on some parts

## Step Files
[xy_cable_chain_back_adxl_opt](assets/xy_cable_chain_back_adxl_opt.stp)

[xy_cable_chain_extruder_mount_std](assets/xy_cable_chain_extruder_mount_std.stp)

[xy_cable_chain_extruder_mount](assets/xy_cable_chain_extruder_mount.stp)

[xy_cable_chain_xy_joiner_hood](assets/xy_cable_chain_xy_joiner_hood.stp)

[xy_cable_chain_xy_joiner](assets/xy_cable_chain_xy_joiner.stp)

[xy_cable_chain_stepper_slider](assets/xy_cable_chain_stepper_slider.stp)

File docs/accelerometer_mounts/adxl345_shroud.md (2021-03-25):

---
title: Oranginator's ADXL345 shroud mount
---

> Created by: [Steffen Brandner](https://github.com/Oranginator)

## Description
Universal Accelerometer Mount for ADXL345 mounted at the EVA-shroud.

Oranginator's ADXL345 shroud mount

## BOM
| No | Qty | Name | Printable |
| -- | --- | --- | --- |
| 1  | 1 | ADXL345 Shroud | [Yes](stl/adxl345_shroud.STL) |
| 2  | 2 | DIN 912 M3 6 mm | No |
| 3  | 1 | AXDL345 | No |
| 4  | 2 | M3 Nut 		 | No |
| 5  | 2 | M3 nylon washer 	  	| No |

## Compatible EVA version
2.0 and newer.

## Print instructions
Print it so that the EVA-logo is flat on the bed.

## Step Files
You can find the STEP-File at [Oranginator's ADXL345 shroud mount](assets/adxl345_shroud.STEP)

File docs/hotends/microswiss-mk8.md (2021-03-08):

---
title: Boont's MK8 Hotend Mount
---

> Created by: [Boont](https://github.com/silvalis)

## Description
This is a MK8 mount for the Microswiss MK8 hotend. It should
work with all mk8 2-bolt hotends.

microswiss-mk8

## Compatible EVA version
2.1.0 - 2.2.0

## Related EVA parts
universal_face
mosquito_support

## Changelog
v1.0 03/03/2021 Boont Release

## BOM:
| No | Qty | Name | Printable |
| -- | --- | --- | --- |
| 1  | 1 | eva-2.2-mk8-hotend.stl | [Yes](stl/eva-2.2-mk8-hotend.stl) |

## Additional files required
Get the mosquito_support.stl from the original [EVA 2.2 stls](https://main.eva-3d.page).

## Hardware Required 
Standard EVA

## To Do 
modify mosquito_support specific for mk8

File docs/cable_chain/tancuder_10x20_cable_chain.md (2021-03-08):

---
title: Mikkel's Cable Chain EVA mount and frame anchor
---

## Description

> Created by: [Mikkel Schmidt](https://github.com/miklschmidt)

A cable chain carriage mount and frame anchor for the [10x20 TANCUDER drag chain found on amazon.de](https://www.amazon.de/gp/product/B07VGC8QJR/)

tancuder_10x20_cable_chain

The EVA carriage mount part replaces the Universal Cable Mount for the EVA Back. You will need 3x M3x10mm and 3 M3 hex nuts for attaching the mount to the EVA back.

You might need another hole pattern for your particular drag chain, if you adapt this design or create a new one, please submit it via pull request! Step files are at the bottom of this page.

## Compatible EVA version
1.1 and newer.

## BOM
| No | Qty | Name | Printable |
| -- | --- | --- | --- |
| 1  | 5 | M3 x 10mm | No |
| 1  | 2 | M3 x 25mm | No |
| 2  | 7 | M3 Hex nuts | No |
| 3  | 4 | M3 Washer | No |
| 6  | 1 | 2020 Frame Anchor | [Yes](stl/tancuder_10x20_cable_chain_2020_frame_anchor.stl) |
| 6  | 1 | EVA Carriage Mount | [Yes](stl/tancuder_10x20_cable_chain_eva_mount.stl) |

## Print instructions
Follow the general EVA guidelines. At least 2 perimeters and 20% infill at .2mm or .3mm layer height. Find a big flat surface to go against the build plate.

## Step Files
[2020 Frame Anchor](assets/tancuder_10x20_cable_chain_2020_frame_anchor.step)

[EVA Carriage Mount](assets/tancuder_10x20_cable_chain_eva_mount.step)

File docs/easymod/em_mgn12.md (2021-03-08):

---
title: Easymod mgn12
---

> Created by: [EOliveira](https://github.com/EduardoOliveira)

## An implementation of MGN12 for EasyMod 1.2.1

The XY joiners are a drop in replacement for the official ones.

This will allow you to use your setup with mgn12 in the X axis, mainly reducing the weight of it.

[Onshape](https://cad.onshape.com/documents/8559b0e7f5d3b30427c227c5/w/d70f098c5b327e06a1ae23f4/e/12a2436a47701eb37945bb45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)

xyjoinners

If you are also using MGN12C or MGN12H on the Y axis you'll need the following adapters in place of the original aluminum plates.

You'll need longer M5 screws as these adapters are 3mm thicker than the aluminum part. I recommend printing with more tops/bottoms and higher infill to incease strength.

xyjoinners

[Onshape](https://cad.onshape.com/documents/8559b0e7f5d3b30427c227c5/w/d70f098c5b327e06a1ae23f4/e/67166bbf807ca01f4a1ac8b3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).

## Compatible EVA versions
1.2.1
## BOM

| No | Qty | Name | Printable |
| -- | --- | --- | --- |
| 1  | 1 | XY Joinner Right | [Yes](stl/XY_Joiner_mgn12_xy_joiner_right.stl) |
| 2  | 1 | XY Joinner Left | [Yes](stl/XY_Joiner_mgn12_xy_joiner_left.stl) |
| 3  | 1 | Joinner plateA C or H | [Yes (mgn12c)](stl/Joiner_Plates_mgn12C_A.stl) / [Yes (mgn12h)](stl/Joiner_Plates_mgn12H_A.stl) |
| 4  | 1 | Joinner plateB C or H | [Yes (mgn12c)](stl/Joiner_Plates_mgn12C_B.stl) / [Yes (mgn12h)](stl/Joiner_Plates_mgn12H_B.stl) |

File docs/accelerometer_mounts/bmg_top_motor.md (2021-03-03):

---
title: Tomasz's BMG top motor mounted ADXL345
---

> Created by: [Tomasz Paluszkiewicz](https://github.com/tomaski)

## Description
An accelerometer mount atop the BMG stepper motor.

Design incorporates a groove under the place where header pins poke down, to be able to lay the accelerometer flat on the mount.

tomaszs_top_BMG

## BOM
| No | Qty | Name | Printable |
| -- | --- | --- | --- |
| 1  | 1 | adxl345-bmg | [Yes](stl/adxl345-bmg.stl) |
| 2  | 2 | DIN 912 M3 25 mm | No |
| 3  | 1 | AXDL345 | No |
| 4  | 2 | ISO 7380 M3 6 mm | No |

## Compatible EVA version
2.0 and newer.

## Print instructions
Print it vertically. 2 shells, 20-30% infill and 0.2 layer height should be fine.

## Step Files
you can export step files from [OnShape](https://cad.onshape.com/documents/25c852bf174fbdf476467b52/v/f168eee5558a37dc260507f3/e/d743a2d0acb3b21eb506a551)

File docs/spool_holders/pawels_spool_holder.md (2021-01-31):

---
title: Paweł's 3030/2020 Spool Holder
---

> Created by: [Paweł Kucmus](https://main.eva-3d.page)

A spool holder with a screw, knob and a filament guide.

You can get different lengths of the screw thread and ends for different 
bearings (608 or 688) you can get those from 
[Onshape](https://cad.onshape.com/documents/c347782b8c92b21780d96bef/w/b88421730fcb90f0d84e16bb/e/4df0478d09f36656e6b06300).

| No | Qty | Name | Printable |
| -- | --- | --- | --- |
| 1  | 2 | M3 x 12mm | No |
| 2  | 2 | M3 Hen nuts | No |
| 3  | 3 | M8 Hen nuts | No |
| 4  | 1 | M8 threaded rod (screw thead length + 90mm) | No |
| 5  | 2 | 608 or 688 bearings | No |
| 6  | 1 | Arm 3030 / 2020 | [Yes (3030)](stl/3030_2020_spool_holder_arm_3030.stl) / [Yes (2020)](stl/3030_2020_spool_holder_arm_2020.stl) |
| 7  | 1 | Guide | [Yes](stl/3030_2020_spool_holder_guide.stl) |
| 8  | 1 | Screw (90mm) | [Yes](stl/3030_2020_spool_holder_screw_90mm.stl) |
| 9  | 1 | Knob | [Yes](stl/3030_2020_spool_holder_knob.stl) |

not_cube

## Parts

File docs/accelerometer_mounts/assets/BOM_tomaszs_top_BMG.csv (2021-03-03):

Item | Quantity | Name | Material
1 | 1 | adxl345-bmg | PETG
2 | 2 | DIN 912 M3 25 mm | Hardened Alloy Steel
3 | 1 | Part 1 | - None -
4 | 1 | Part 2 | - None -
5 | 2 | ISO 7380 M3 6 mm | - None -

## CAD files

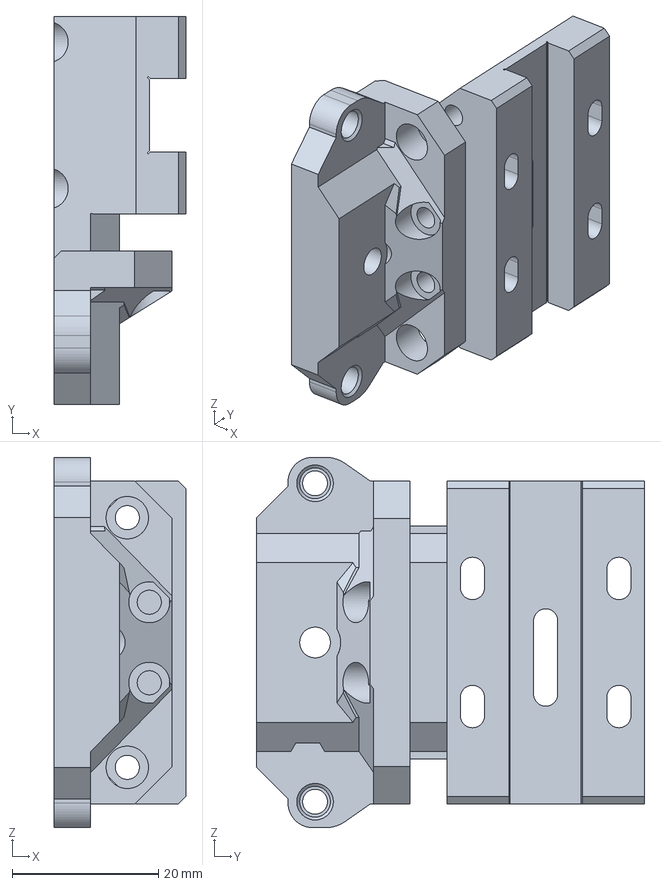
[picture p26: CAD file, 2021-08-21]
docs/extruders/assets/pcr-sherpa-mini-main-mount.step
18.0 x 53.0 x 50.6 mm

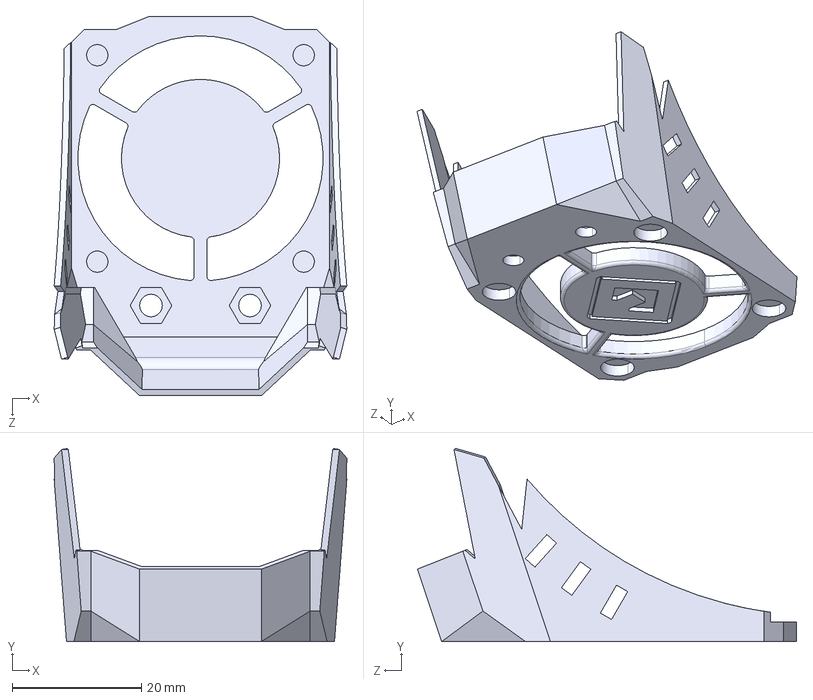
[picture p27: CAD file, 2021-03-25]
docs/accelerometer_mounts/assets/adxl345_shroud.STEP
45.4 x 29.9 x 58.7 mm

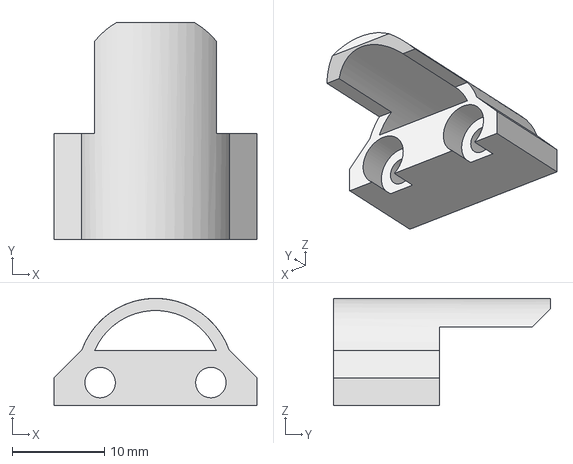
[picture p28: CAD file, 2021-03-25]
docs/cable_chain/assets/xy_cable_chain_stepper_slider.stp
22.0 x 23.5 x 11.6 mm

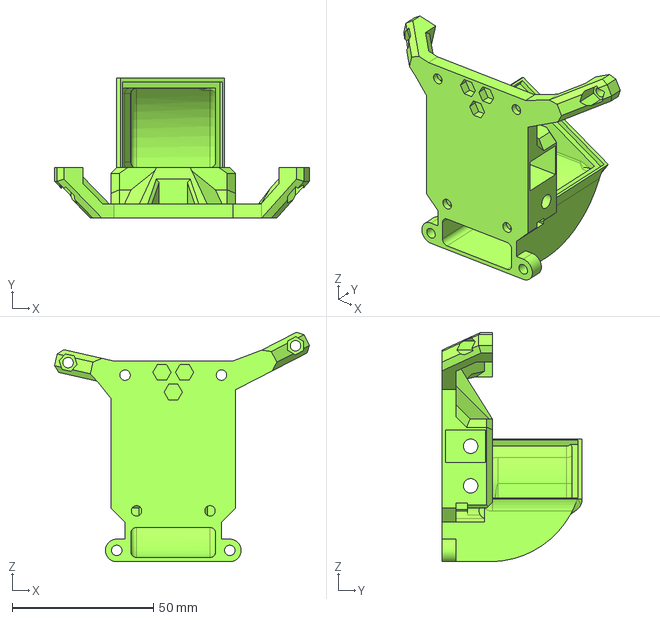
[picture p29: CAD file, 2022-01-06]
docs/cooling/assets/7530_part_fan_remix.step
90.2 x 49.6 x 81.2 mm

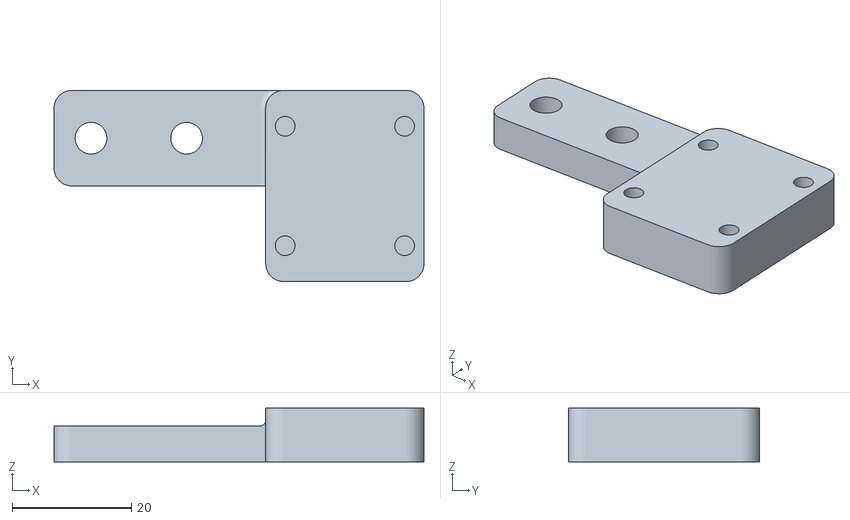
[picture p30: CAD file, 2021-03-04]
docs/easymod/stl/Joiner_Plates_mgn12H_B.stl
61.9 x 32.0 x 9.00

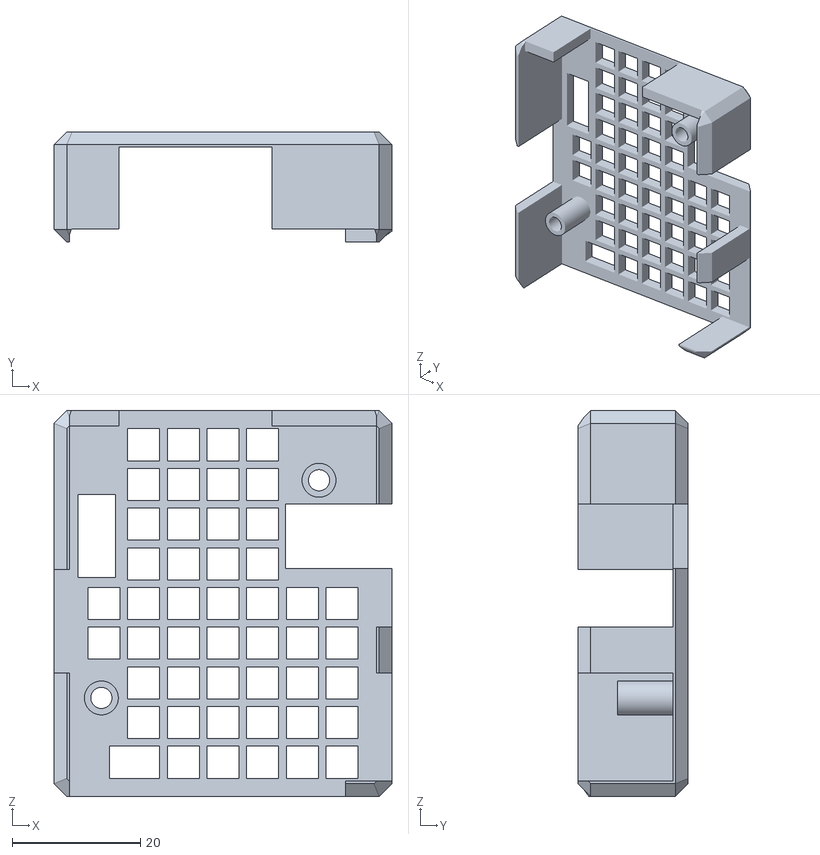
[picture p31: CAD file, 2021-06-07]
docs/electronics/stl/duet3_toolboard_1lc_v11_lid.stl
52.8 x 17.2 x 60.3

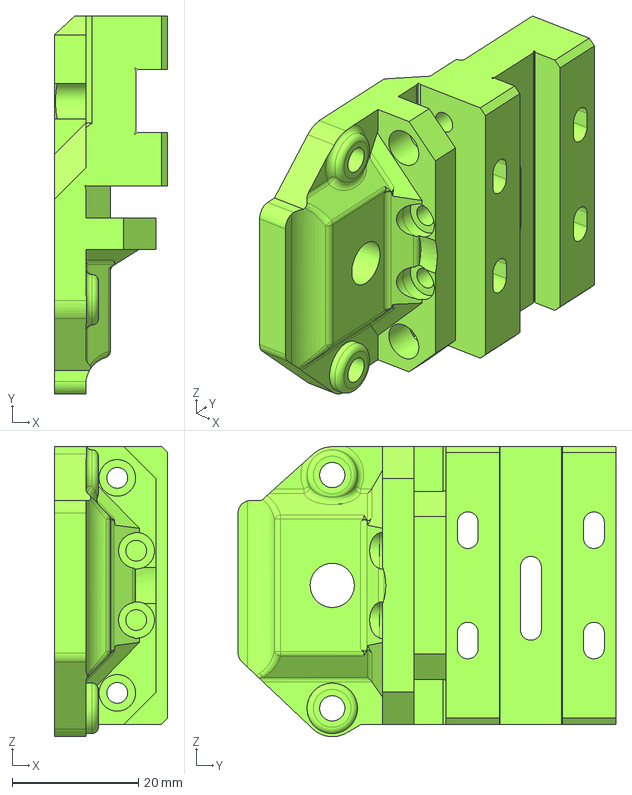
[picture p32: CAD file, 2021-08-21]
docs/extruders/assets/E3D-V6-Orbiter-2.85mm.stp
18.0 x 60.0 x 46.0 mm

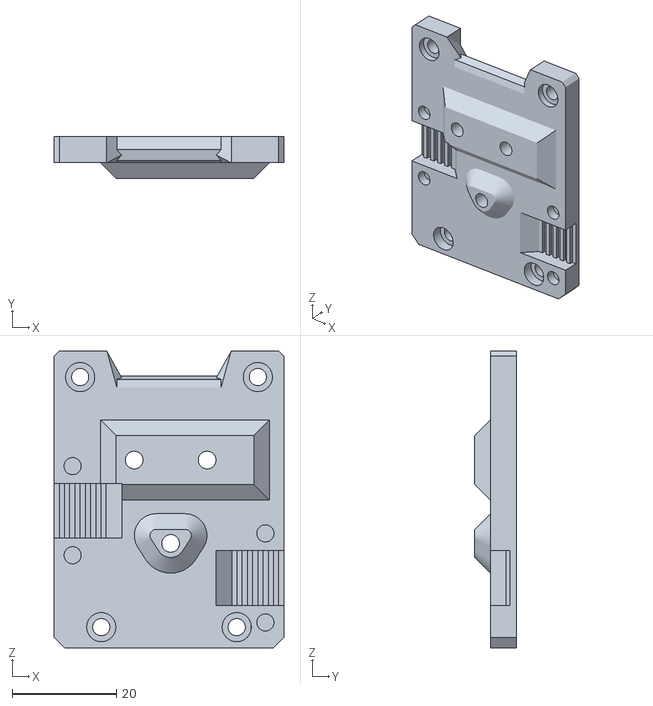
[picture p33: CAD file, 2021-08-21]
docs/extruders/stls/Mellow-Sunrise-Front-Plate-Volcano.stl
44.1 x 8.00 x 57.0

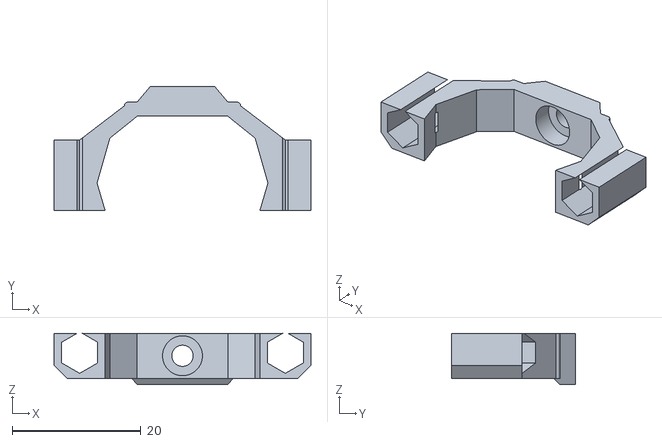
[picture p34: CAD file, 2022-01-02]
docs/hotends/stl/eva-2.3-dragonfly-HIC-support.stl
40.0 x 19.4 x 8.00

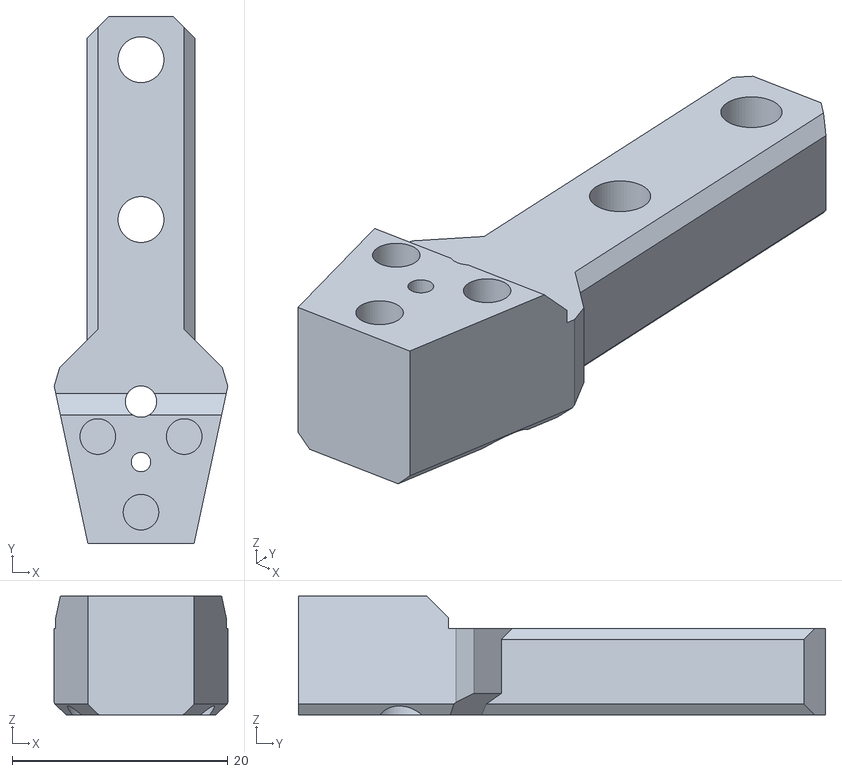
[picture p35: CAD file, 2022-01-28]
docs/mounts-with-brass-inserts/stl/unversal_cable_mount-2.4.2-inserts.stl
16.1 x 48.8 x 11.0

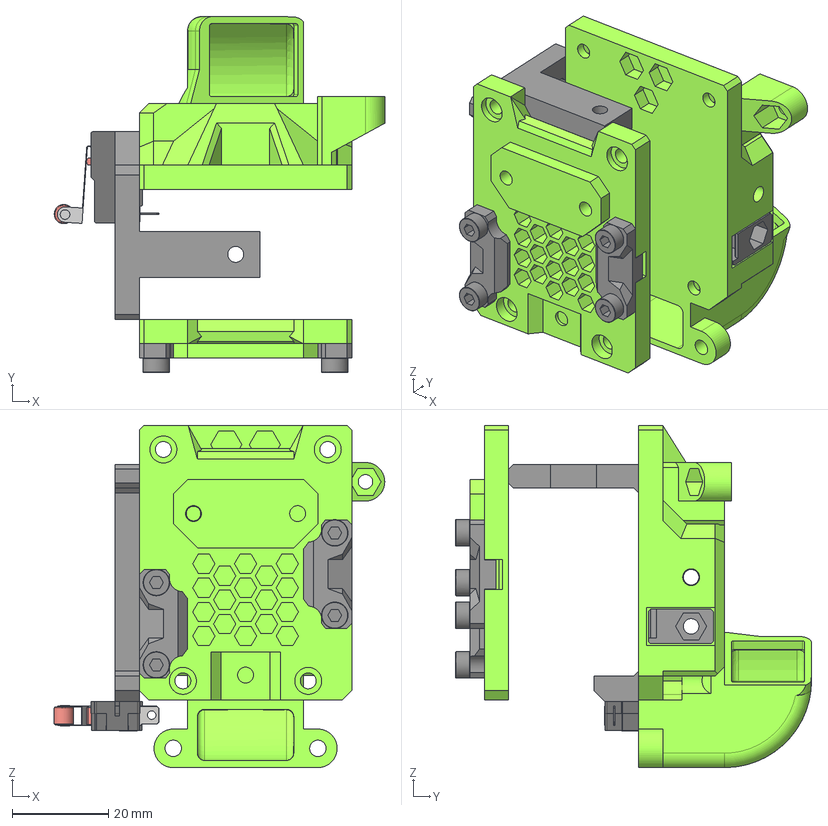
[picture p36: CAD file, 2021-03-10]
docs/printer-compatibility/assets/blv-mgn-cube.step
68.6 x 73.8 x 71.0 mm
back_corexy
Tension Sliders M3 - tension_slider_6mm_belt_M3_mirror (low) v1
Tension Sliders M3 - tension_slider_6mm_belt_M3 v1
top_endstop_plug_mgn12
Button(Mirror)
Lever(Mirror)
Wheel(Mirror)
DIN 912 M3 8 mm x 4
face_belt_grabber x 2
M3 Hex nut x 4
universal_face

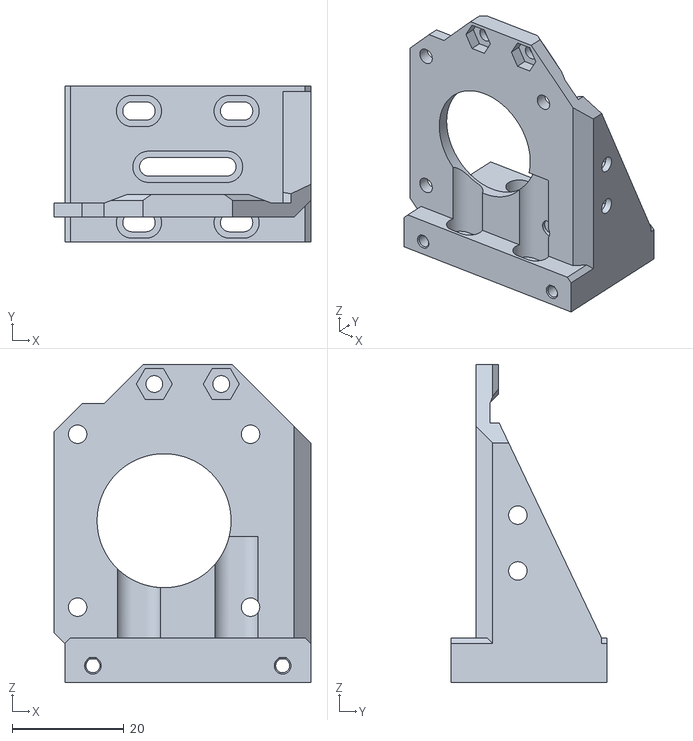
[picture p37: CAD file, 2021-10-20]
docs/printer-compatibility/stl/EVA_MC_top_bmg_mgn12.stl
46.0 x 28.0 x 57.0

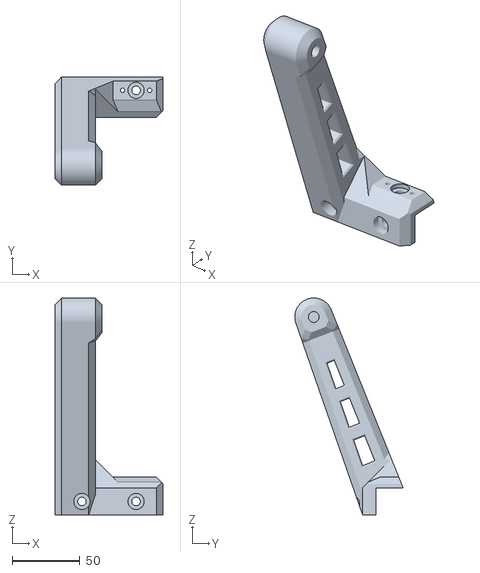
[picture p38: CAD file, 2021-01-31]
docs/spool_holders/stl/3030_2020_spool_holder_arm_2020.stl
80.0 x 80.0 x 160.2

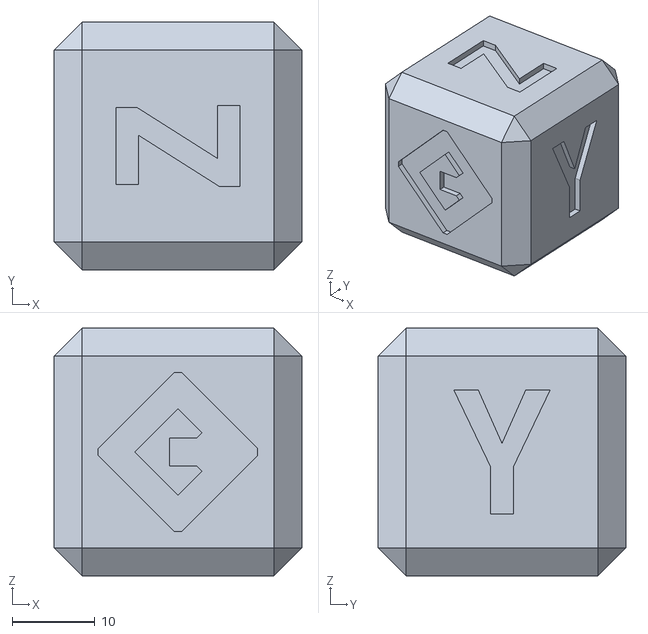
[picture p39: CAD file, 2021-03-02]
docs/test_prints/stl/eva_30mm_calibration_cube.stl
30.0 x 30.0 x 30.0

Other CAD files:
docs/extruders/stls/pcr-sherpa-mini-main-mount.stl
docs/accelerometer_mounts/stl/adxl345_shroud.STL
docs/cable_chain/stl/xy_cable_chain_stepper_slider.stl
docs/cooling/stl/7530_part_fan_remix.stl
docs/accelerometer_mounts/stl/adxl345-bmg.stl
docs/cable_chain/assets/dual_5015_part_fan_cable_chain.stp
docs/cable_chain/assets/dual_5015_part_fan_cable_chain_frame.stp
docs/cable_chain/assets/tancuder_10x20_cable_chain_2020_frame_anchor.step
docs/cable_chain/assets/tancuder_10x20_cable_chain_eva_mount.step
docs/cable_chain/assets/xy_cable_chain_back_adxl_opt.stp
docs/cable_chain/assets/xy_cable_chain_extruder_mount.stp
docs/cable_chain/assets/xy_cable_chain_extruder_mount_std.stp
docs/cable_chain/assets/xy_cable_chain_xy_joiner.stp
docs/cable_chain/assets/xy_cable_chain_xy_joiner_hood.stp
docs/cable_chain/stl/dual_5015_part_fan_cable_chain.stl
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

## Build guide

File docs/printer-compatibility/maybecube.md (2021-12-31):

---
title: EVA conversion kit for the MaybeCube
---

> Created by: [Martin Budden](https://github.com/martinbudden)

## Description

Adaptors to allow the  [EVA printheads](https://main.eva-3d.page/) to be used on the [MaybeCube 3D printer](https://github.com/martinbudden/MaybeCube).

Since the belt spacing used by the EVA system is different to that used by the MaybeCube, adaptors are required: an adaptor for the EVA top part and an adaptor for the EVA bottom part.

The bottom adaptor is **EVA\_MC\_bottom\_mgn12\_short\_duct.stl**.

The top adaptor varies according to the extruder used - the part name is the same as the EVA part, but prefixed by **EVA\_MC\_**. So for example if you wanted to used the Bondtech BMG extruder then you should use part **EVA\_MC\_bmg\_mgn12.stl** (rather than part **bmg\_mgn12.stl** that you would ordinarily use).

Once you have installed the top and bottom adaptors, you can use all other EVA parts in the normal way.

The photos show an EVA printhead with adaptors for the Bondtech BMG extruder.

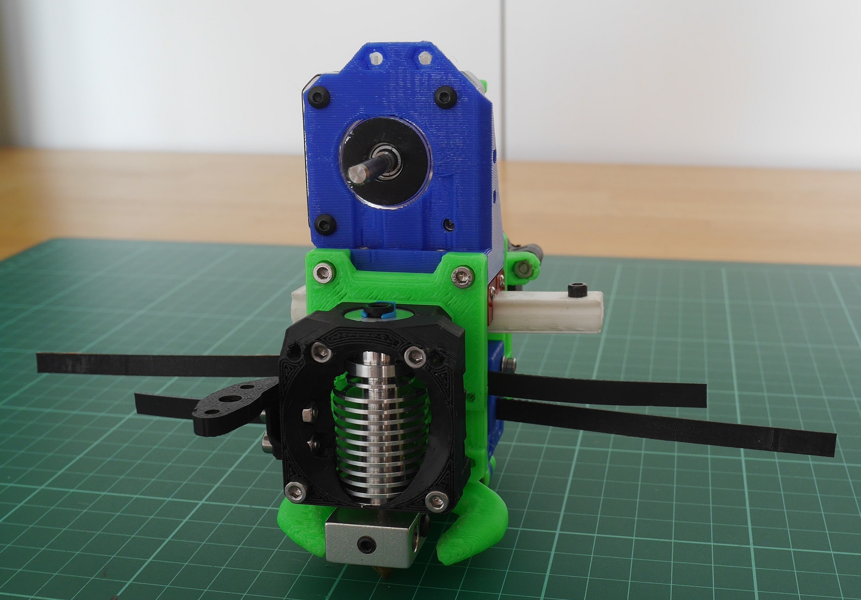
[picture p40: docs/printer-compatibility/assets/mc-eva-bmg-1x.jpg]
MC EVA BMG 1


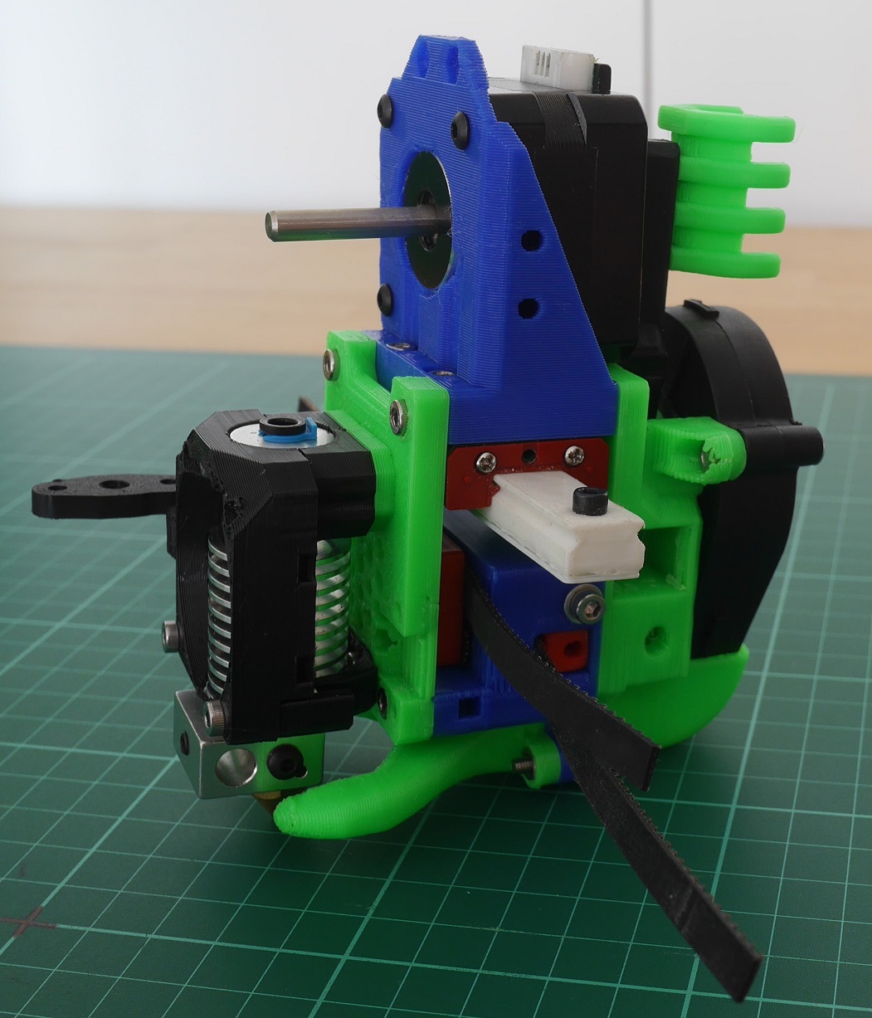
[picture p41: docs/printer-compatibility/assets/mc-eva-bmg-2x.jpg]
MC EVA BMG 2


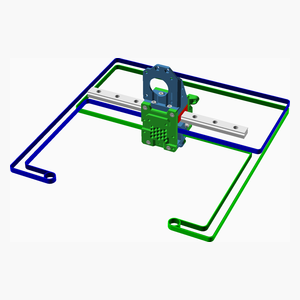
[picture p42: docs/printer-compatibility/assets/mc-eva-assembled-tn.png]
MC EVA BMG assembled


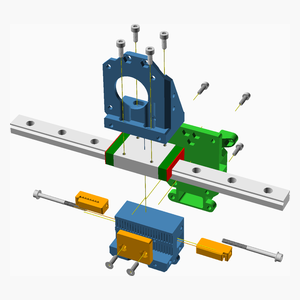
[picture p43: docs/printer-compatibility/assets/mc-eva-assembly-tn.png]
MC EVA BMG assembly


In the pictures the adaptors are shown in blue, standard  EVA parts are shown in green and black, and MaybeCube parts are shown in red or orange.

Assembly instructions are on [github](https://github.com/martinbudden/MaybeCube/tree/main/EVA).

[Thingiverse link](https://www.thingiverse.com/thing:4912099)

## Compatible EVA version

2.3.0

## BOM

| No | Qty | Name | Printable |
| -- | --- | --- | --- |
| 1  | 1 | MC bottom adaptor | [Yes](stl/EVA_MC_bottom_mgn12_short_duct.stl) |
| 2  | . | MC top Bondtech BMG adaptor | [Yes](stl/EVA_MC_top_bmg_mgn12.stl) |
| 3  | . | MC top Bondtech LGX adaptor | [Yes](stl/EVA_MC_top_lgx_mgn12_a.stl) |
| 4  | . | MC top Bowden adaptor | [Yes](stl/EVA_MC_top_mgn12.stl) |
| 5  | . | MC top Orbiter adaptor | [Yes](stl/EVA_MC_top_orbiter_mgn12.stl) |
| 6  | . | MC top E3D Titan adaptor | [Yes](stl/EVA_MC_top_titan_mgn12.stl) |
| 7  | 8 | M3 caphead bolt x 10mm | No |

Note that the bolts self-tap into adaptor parts.
Standard EVA parts and MaybeCube parts are not shown in the BOM.

The E3D Hemera and E3D Aero extruders are not currently supported.

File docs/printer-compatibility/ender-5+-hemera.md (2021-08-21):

---
title: Poko's Ender 5+ & Hemera Faceplate
---

> Created by: [Poko](https://github.com/lorentzkim)

## Description
This is a modification of Hemera faceplate v2.3 for Ender 5+.

It shifts the beltgrabber slots central to the 2020 extrusion on a Ender 5+ 
printer modified with MGN12H linear rail mounted on top.

It's essentially a mix between Hemera faceplate and Boont's Ender 5/5+ mod.

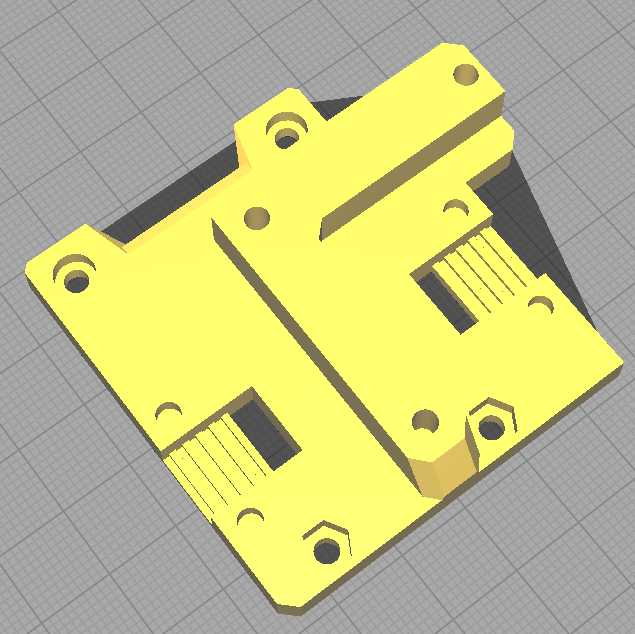
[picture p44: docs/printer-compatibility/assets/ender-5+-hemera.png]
cura render

## Compatible EVA version
2.3+?

## Changelog
v1.0 26/06/2021 Initial release

## Related EVA parts
This replaces `hemera_face.stl`.

Please see [Boont's](https://contrib.eva-3d.page/printer-compatibility/ender-5/)
mod for the Ender 5 flat back. Like his, this change should be compatible with
standard CoreXY backplate.

## BOM
| No  | Qty | Name | Printable |
| --- | --- | --- | --- |
| 1 | 1 | ender-5+-hemera-face | [Yes](stl/ender-5+-hemera-face.stl) |

## Additional files required
Get the belt grabbers from the original [EVA stls](https://main.eva-3d.page).

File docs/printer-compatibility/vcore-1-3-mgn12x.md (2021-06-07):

---
title: V-Core Pro 1.3 MGN12C or MGN12H
---

> Created by: [EOliveira](https://github.com/EduardoOliveira)

## Description
An implementation of the V-Core Pro 1.3 kinematic design using MGN12C or MGN12H

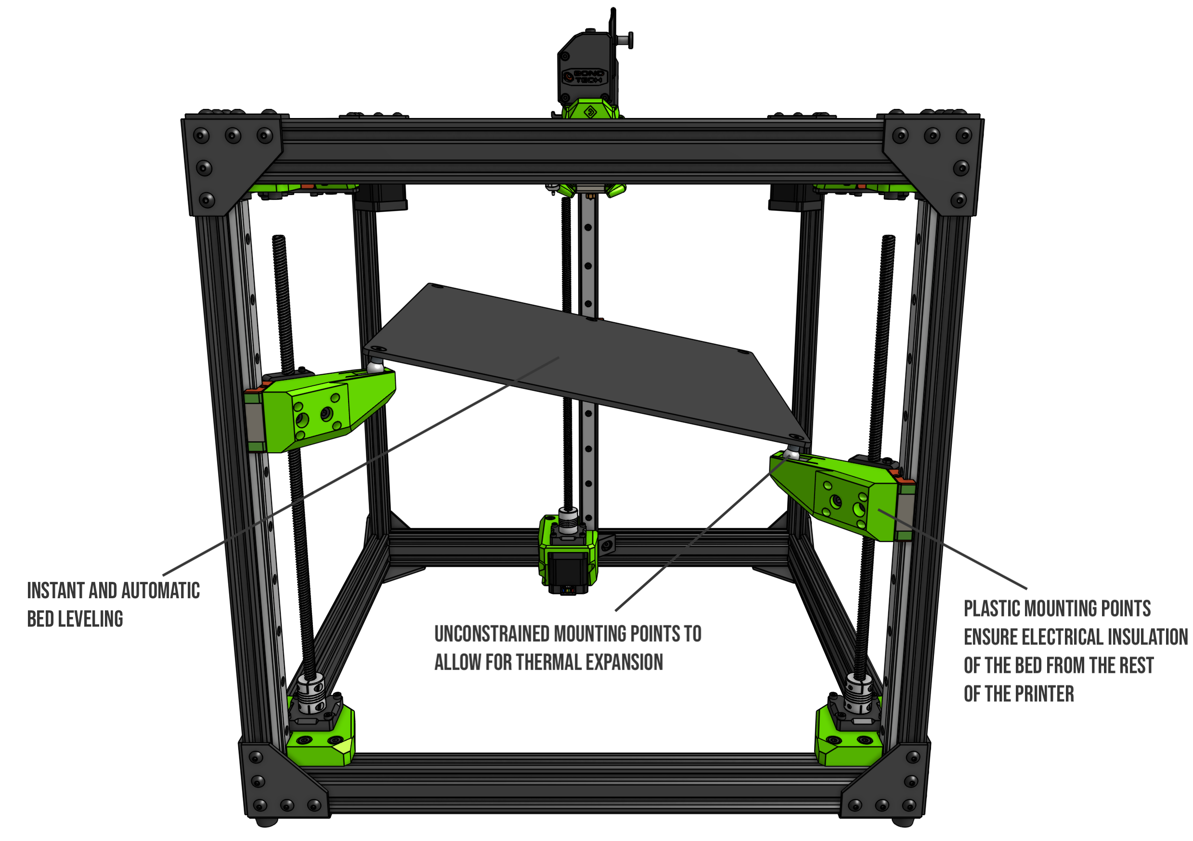
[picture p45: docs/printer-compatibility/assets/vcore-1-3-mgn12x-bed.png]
1.3bed


## Compatible EVA version
Any

## BOM
| No | Qty | Name | Printable |
| -- | --- | --- | --- |
| 1  | 1 | Back Arm C or H | [Yes (mgn12c)](stl/Bed-Arms-back-MGN12C.stl) / [Yes (mgn12h)](stl/Bed-Arms-back-MGN12H.stl) |
| 2  | 1 | Left Arm C or H | [Yes (mgn12c)](stl/Bed-Arms-front-left_arm-MGN12C.stl) / [Yes (mgn12h)](stl/Bed-Arms-front-left_arm-MGN12H.stl) |
| 3  | 1 | Right Arm C or H | [Yes (mgn12c)](stl/Bed-Arms-front-right_arm-MGN12C.stl) / [Yes (mgn12h)](stl/Bed-Arms-front-right_arm-MGN12H.stl) |

## Additional files required
Get the Z motor mounts and cable strain relief from [V-Core-Pro-1.3 github](https://github.com/Rat-Rig/V-Core-Pro-1.3/tree/main/cad/01_essentials/Zaxis/STL).

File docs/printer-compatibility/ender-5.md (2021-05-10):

---
title: Boont's Ender 5/5+ Mod
---

> Created by: [Boont](https://github.com/silvalis)

## Description
This is a modification of the universal faceplace v2.2 for Ender5 family printers. 
It shifts the beltgrabber slots central to the 2020 extrusion on a Ender 5 
printer modified with MGN12H linear rail mounted on top.

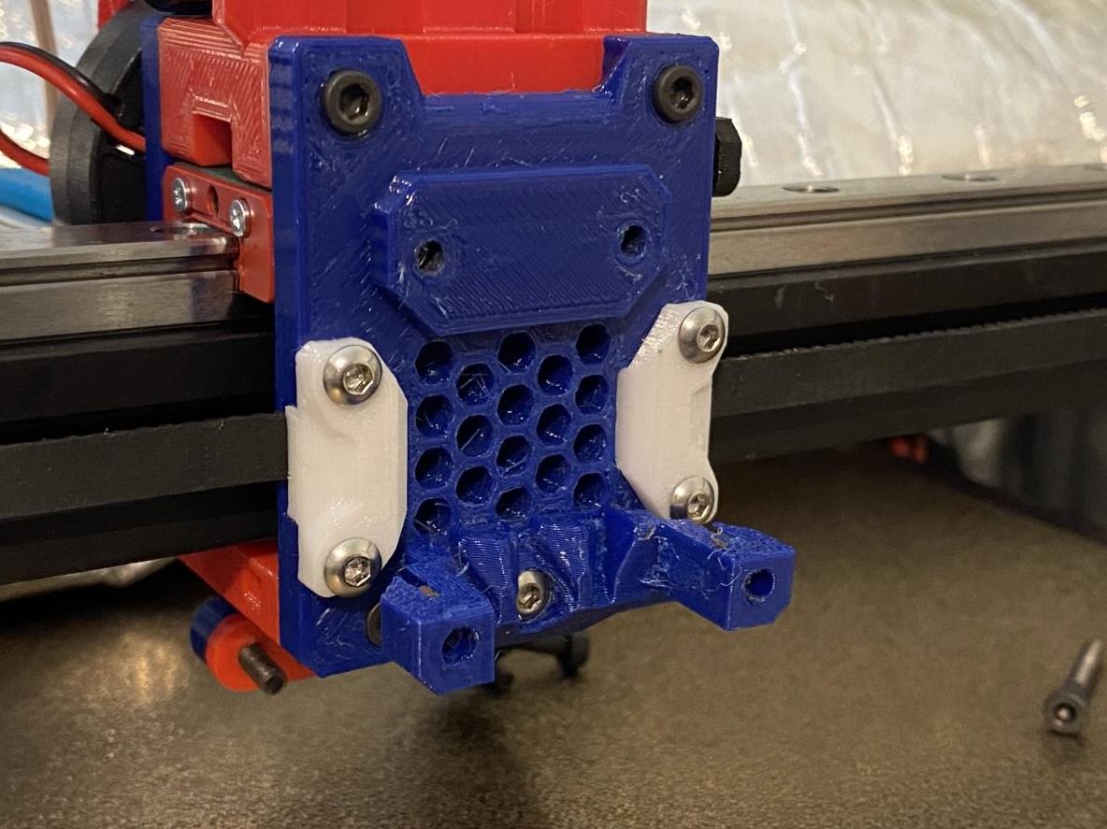
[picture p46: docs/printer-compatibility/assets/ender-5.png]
microswiss-mk8

## Compatible EVA version
2.1.0 -> 2.2.X

## Changelog:
v1.0 03/03/2021 Boont Release
v1.1 19/04/2021 FlatESIAN back plate added

## Related EVA parts
This replaces the universal_face

This works in conjunction with a flattened backplate to preserve rear space on an 
Ender 5, however blocks the use of the vertical cable guide. The Ender 5 Plus may
use the standard corexy backplate if you wish to use the cable guide.

## BOM
| No | Qty | Name | Printable |
| -- | --- | --- | --- |
| 1  | 1 | eva-2.2-ender-5-universal-face | [Yes](stl/eva-2.2-ender-5-universal-face.stl) |
| 1  | 1 | eva-2.2-ender-5-flat-back 		| [Yes](stl/eva-2.2-ender-5-flat-back.stl) |

## Additional files required
Get the belt grabbers from the original [EVA 2.2 stls](https://main.eva-3d.page).

## To Do
Modify the vertical cable guide stalk to clear the flatESIAN back

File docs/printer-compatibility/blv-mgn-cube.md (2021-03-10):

---
title: EVA conversion kit for BLV MGN Cube
---

> Created by: [tetele](https://github.com/tetele)

Mounting kit for the [EVA v2](https://eva-3d.github.io/eva-main/) on the [BLV MGN Cube printer](https://www.blvprojects.com/blv-mgn-cube-3d-printer).

The standard EVA hotend carriage was designed for printers using 9mm belts with a different orientation than the BLV MGN Cube. This kit provides all the parts needed to use the EVA on the BLV MGN Cube.

| No | Qty | Name | Printable |
| -- | --- | --- | --- |
| 1  | 1 | Modified universal face | [Yes](stl/blv-ngm-cube-universal_face.stl) |
| 2  | 2 | 6mm belt grabbers | [Yes](stl/blv-mgn-cube-face_belt_grabber.stl) |
| 3  | 1 | Modified CoreXY back | [Yes](stl/blv-mgn-cube-back_corexy.stl) |
| 4  | 1 | 6mm belt tensioner (left) | [Yes](stl/blv-mgn-cube-tension_slider_6mm_left.stl) |
| 5  | 1 | 6mm belt tensioner (right) | [Yes](stl/blv-mgn-cube-tension_slider_6mm_right.stl) |
| 6  | 1 | End stop microswitch mount | [Yes](stl/blv-mgn-cube-end_stop_mount.stl) |

The kit only supports hotends and extruders that are compatible with the original universal face (e.g. not the Titan Aero, which has a dedicated face). It also only supports 6mm timing belts.

[Thingiverse link](https://www.thingiverse.com/thing:4718073)

If you want to remix things, the [STEP files are here](assets/blv-mgn-cube.step).

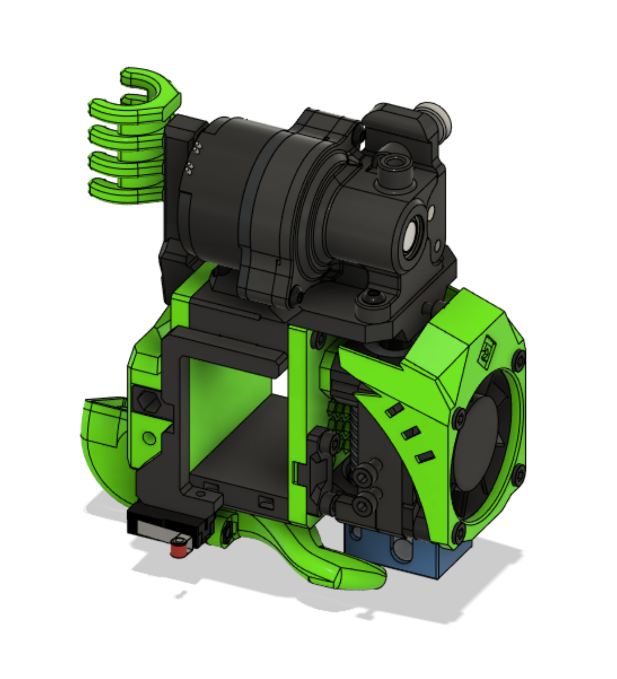
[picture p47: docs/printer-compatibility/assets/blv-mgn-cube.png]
EVA BLV MGN Cube conversion kit


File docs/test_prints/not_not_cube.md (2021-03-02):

---
title: Mikkel's Not Not Cube
---

> Created by: [Mikkel Schmidt](https://github.com/miklschmidt)

Just another simple test print.

[Download :octicons-download-24:](stl/eva_30mm_calibration_cube.stl){: .md-button .md-button--primary }

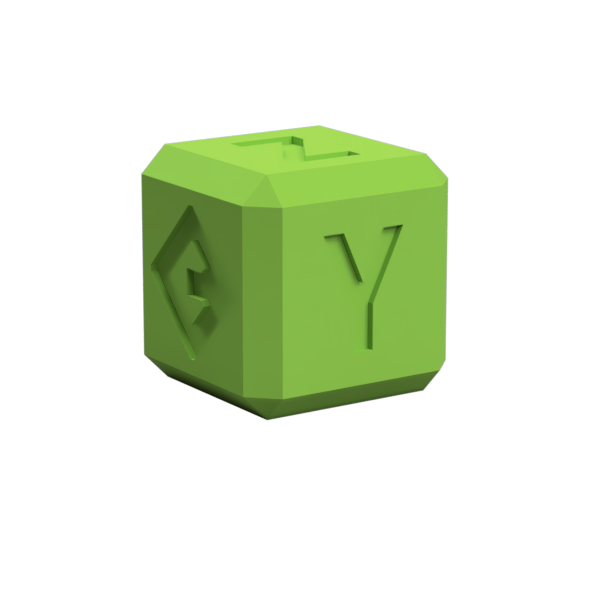
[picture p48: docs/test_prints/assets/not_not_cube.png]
not_cube


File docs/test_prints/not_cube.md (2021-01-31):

---
title: Paweł's Not Cube
---

> Created by: [Paweł Kucmus](https://main.eva-3d.page)

Just a simple test print.

[Download :octicons-download-24:](stl/test_cube_ball_thingy.stl){: .md-button .md-button--primary }

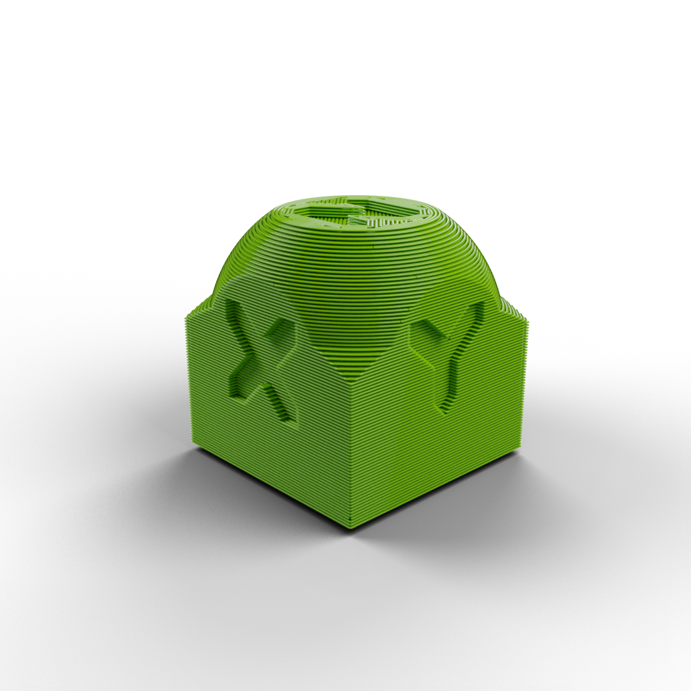
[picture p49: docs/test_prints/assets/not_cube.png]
not_cube


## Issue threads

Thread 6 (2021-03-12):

EVA Dual 5015 Part Fan MOD

SuperSniffles, 2021-03-12:
## Part name
EVA Dual 5015 Part Fan MOD

## Compatible EVA version
2.0.0 --> 2.2.1
## Related EVA parts

Replaces:
back_corexy
top_bmg_mgn15
adds:
top_bmg_mgn15_2x5015_Mod
back_corexy_2x5015_Mod
Cable_Chain_Mount_2x_5015_BMG
Cable_Chain_Mount_2x_5015_Frame

## Necessary Hardware BOM
2x 5015 Blower Fan
some M3 Screws

## Description
This Dual 5015 Part Fan mod replaces the single 5015 Part Fan located on the backplate with 2 5015 Part Fans moved to the sides. The mod is intended to supply a higher cooling capacity than the standard setup.

## Onshape or STEP files
files are attached

## Print instructions
LH = 0.2
Nozzle = 0.4
Supports needed

## Contributor
Supersniffles.

[5015.zip](https://github.com/EVA-3D/contrib-extras/files/6132507/5015.zip)

miklschmidt, 2021-03-16:
Thank you!

Finally got around to add it (see EVA-3D/contrib-extras@85afc9e)!

Check it [here](https://contrib.eva-3d.page/cooling/dual_5015_part_fan/) and [here](https://contrib.eva-3d.page/cable_chain/dual_5015_part_fan_cable_chain/)

Closed 2021-03-16.

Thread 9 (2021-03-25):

XY Cable Chain Mod

SuperSniffles, 2021-03-25:
Part name
EVA Dual 5015 Part Fan MOD

Compatible EVA version
2.0.0 --> 2.2.1

Related EVA parts

Replaces:
none

adds:
XY_BMG_Mount (use this if you already use my 5015 dual fan mod)
XY_BMG_Mount_Std (use this for the original setup with one fan on the back)
XY_Chain_stepper_slider
XY_Back_ADXL_opt (optional if you want to use ADXL)
XY_Mount_clip-20
XY_Mount_clip-20_Hood

Necessary Hardware BOM
Cable Chain https://www.amazon.de/gp/product/B07VGC8QJR/ref=ppx_yo_dt_b_asin_title_o00_s00?ie=UTF8&psc=1
some M3 Screws
some M5 Screws
some drop in T-Nuts

Description
This Mod adds XY cable cain support to the V-Core. Nothing more to say.
[XY.zip](https://github.com/EVA-3D/contrib-extras/files/6207977/XY.zip)

Onshape or STEP files
files are attached

Print instructions
LH = 0.2
Nozzle = 0.4
Supports needed

Contributor
Supersniffles.

miklschmidt, 2021-03-25:
Done.

Closed 2021-03-25.

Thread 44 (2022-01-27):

With 40x20 hotend fan, Eva touches frame

ManuelPeiro, 2022-01-27:
In a Ratrig v3 400, for try avoid heatcreep issues, I have instaled a 40x20, onstead of the default 4010.

When I move Eva to Y max, narrowly, but touch the frame of the printer, maybe 2 or 3 mm

**To Reproduce**

1 install a 40x20 heatskin fan
2 move Eva to Y Max

**Expected behavior**
Eva dont touch frame

**Screenshots**

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

**Desktop (please complete the following information):**
 - OS: [e.g. iOS]
 - Browser [e.g. chrome, safari]
 - Version [e.g. 22]

**Smartphone (please complete the following information):**
 - Device: [e.g. iPhone6]
 - OS: [e.g. iOS8.1]
 - Browser [e.g. stock browser, safari]
 - Version [e.g. 22]

**Additional context**
Add any other context about the problem here.

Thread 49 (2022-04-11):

Can we make CAD files mandatory?

JonDum, 2022-04-11:
There are huge gaps in quality between some of the contributions and with all the changing bits and pieces from EVA main it becomes very, very irritating to try and decipher how some of these are supposed to work and/or improve them.

I'm going to pick on @SuperSniffles for a second. Their contributions are friggin awesome and edges, but the docs around them are sparse. Normally I'm not one to complain about that in the open-source world, but with the lack of any "source" here it really kicked me in the nuts 😆

For example, the [XY Cable Chain mod page](https://contrib.eva-3d.page/cable_chain/xy_cable_chain_mod/) has a single picture of the front, but doesn't show how the various pieces fit in the carriage. Even looking at the step files I couldn't figure it out.

What was throwing me for a loop was this:

> This mod has only been tested with a BMG setup, but should work with all top mounted extruders.

Turns out that's not the case at all. The mod seems to work with *only* BMG-style extruders (i.e., not Orbiter).

It took me literally [bringing the whole EVA carriage into one OnShape assembly ](https://cad.onshape.com/documents/5e67d395ea5cee2510094d74/w/e0b284628a8cf511be6e329a/e/479175fa3e10a835d3ad3e3e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) for me to figure out how the extruder_mount piece was supposed to work and why it wouldn't work for an Orbiter. I still have no idea how/where `xy_cable_chain_stepper_slider` goes though.

Just saying could have avoided hours of me fussing around if we just enforce some sort of assembly CAD file like the main EVA project has.

---

Anyways, sorry for the long rant.

I'll gladly add some cleanup to this specific mod if maintainers will have it, but it'd be awesome if we could make that more of a standard going forward as well

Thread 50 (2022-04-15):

parts for Revo SIX

midicdj1000, 2022-04-15:
Hi, I was wondering when the Revo Six parts will be released ? I have swapped over from a V6 and I think my ASA parts have shrunk a bit. Before I had a dragonfly and I was using the v6 mount and everything was ok, but now the lower support section is touching the revo heatsink and the fan was also touching it.. So I will need to print the parts again, but it would be nice to print the actual Revo six parts. I would be happy to test them for you.

Lee

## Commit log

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2021-03-02 Relative paths are being weird
    [tancuder_10x20_cable_chain_2020_frame_anchor.stl, tancuder_10x20_cable_chain_eva_mount.stl]
2021-03-02 Add not not cube test print
    [eva_ 30mm_calibration_cube.stl]
2021-03-02 again with the links...
    [eva_30mm_calibration_cube.stl]
2021-03-03 ADXL345 for BMG top (#2)
    * add axdl345 mount for bmg top
    * adds missing onshape link)
    * fix typo in the description
    [BOM_tomaszs_top_BMG.csv, adxl345-bmg.stl]
2021-03-04 easymod mgn12 (#4)
    * changed contrib name to discord nickname
    * removed the unofficial words as there is no official version yet
    * fixed typos, text changes
    [Joiner_Plates_mgn12C_A.stl, Joiner_Plates_mgn12C_B.stl, Joiner_Plates_mgn12H_A.stl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]
2021-03-08 Add ender 5 mod and mk8 mount
    [Boont-EVA2.2-E5-Universal-Face.stl, Boont-EVA2.2-MK8-Hotend.stl]
2021-03-08 Fix up boont's contributions
    [eva-2.2-ender-5-universal-face.stl, eva-2.2-mk8-hotend.stl]
2021-03-10 EVA conversion kit for the BLV MGN Cube (#5)
    * Initial addition
    * Renamed preview file
    [blv-mgn-cube-back_corexy.stl, blv-mgn-cube-end_stop_mount.stl, blv-mgn-cube-face_belt_grabber.stl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]
2021-03-16 Add dual 5015 mod from @SuperSniffles
    [daul_5015_part_fan_top_bmg_mgn15.stl, daul_5015_part_fan_top_bmg_mgn15.stp, dual_5015_part_fan_cable_chain.stl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]
2021-03-21 Add Oranginator's ADXL345 shroud mount (#7)
    * Accelerometer Shroud Mount by Oranginator
    Universal Accelerometer Mount for ADXL345 mounted at the EVA-shroud.
    * ADXL345 Shroud by Oranginator
    ADXL345 Shroud by Oranginator
    * Add files via upload
    * Update ADXL345 Shroud.md
    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
    [adxl345_shroud.STL]
2021-03-25 Add dual 5015 part fan connector
    [dual_5015_part_fan_connector.stl]
2021-03-25 ... Added STEP file for Oranginator's ADXL345 shroud mount (#8)
    Fix step file reference
    [adxl345_shroud.STEP]
2021-03-25 Fix dual 5015 typos and add connector step
    [dual_5015_part_fan_connector.stp, dual_5015_part_fan_top_bmg_mgn15.stl, dual_5015_part_fan_top_bmg_mgn15.stp]
2021-03-25 Add supersniffles xy cable chain mount
    [xy_cable_chain_back_adxl_opt.stl, xy_cable_chain_back_adxl_opt.stp, xy_cable_chain_extruder_mount.stl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]
2021-03-25 Add V-Core Pro 1.3 mgn12c/h support (#10)
    [Bed-Arms-back-MGN12C.stl, Bed-Arms-back-MGN12H.stl, Bed-Arms-front-left_arm-MGN12C.stl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]
2021-04-04 Sherpa Mini support added (#11)
    Sherpa Mini support added
    MGN12 and MGN15C top plates
    [sherpa-mini-eva2-mgn12.stl, sherpa-mini-eva2-mgn15c.stl]
2021-05-10 Added modded Dragon and Mosquito mounts with brass inserts
    [Dragon-face-insert.stl, Dragon-support-insert.stl, Duct-2.1-straight-wide-high-inserts.stl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]
2021-05-10 Flat back plate added to Ender5 / cartesian fileset (#13)
    Added flat back plate
    [eva-2.2-ender-5-flat-back.stl]
2021-05-11 Added modded Dragon and Mosquito mounts with brass inserts (#14)
    [Dragon-face-insert.stl, Dragon-support-insert.stl, Duct-2.1-straight-wide-high-inserts.stl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]
2021-05-13 Add DragonFly BMS mod
    [[Face] DragonFly BMS M - DragonFly_BMS_support.stl]
2021-05-13 Fix up dragonfly formatting
    [eva-2.2-dragonfly-bms-support.stl]
2021-05-13 Fix sherpa mini stl links
2021-05-13 Add dual 5015 v2 and 7530 fan mods
    [7530_back_corexy.step, 7530_fan_back_corexy.stl, 7530_fan_mgn12_bottom_wide.stl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]
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2021-06-06 Upload STLs for corexy-backplate and universal faceplate
    [back_corexy-heat-insert.stl, universal_face-heat-inserts.stl]
2021-06-06 Add parts for dual fan with heated inserts
    [dual_5015_back_heat-inserts.stl]
2021-06-07 Minor formatting fixes to heat insert remixes
    [dual_5015_back_v2.0_heat_inserts.stl]
2021-06-11 Updated Mounts to v1.2 - Fixed the geometry on Dragon face, improved strength on Mosquito support
    [Dragon-face-insert.stl, Dragon-support-insert.stl, Mosquito-support-inserts.stl]
2021-06-11 New files were missing
    [Dragon-face-insert-1.2.stl, Dragon-support-insert-1.2.stl, Mosquito-support-inserts-1.2.stl]
2021-06-11 file renamed after convention
    [Mosquito-face-inserts-v1.2.stl]
2021-06-11 fixed name
    [Mosquito-face-inserts-v1.2.stl]
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2021-06-26 Add Ender-5+ Hemera faceplate contrib doc + stl
    [ender-5+-hemera-face.stl]
2021-08-04 Mellow Sunrise added
    Added Mellow Sunrise files including STEP assembly files for people to be able to edit/use in their CAD models.
    [Front Plate - Mellow Sunrise Volcano.stl, Front Plate - Mellow Sunrise.stl, Standard Duct - Mellow Sunrise.stl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]
2021-08-04 Removed placeholder for Mellow Wind
    [Front-Plate-Mellow-Sunrise-Volcano.stl, Front-Plate-Mellow-Sunrise.stl, Standard-Duct-Mellow-Sunrise.stl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]
2021-08-09 add compatibility with monster duct and dual 5015
    [Bottom-Wide-Duct-Extended.stl]
2021-08-12 Extended duct section moved to bottom part
    [Bottom-Wide-Duct-Extended.stl, Front-Plate-Mellow-Sunrise-Volcano.stl, Front-Plate-Mellow-Sunrise.stl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]
2021-08-21 Add P-C-R's Sherpa Mini Mount for EVA 2.3
    [sherpa_mini_main_mount.step, sherpa_mini_main_mount.stl, sherpa_mini_motor_holder.step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]
2021-08-21 Fix P-C-R's pull request
    [pcr-sherpa-mini-main-mount.step, pcr-sherpa-mini-main-mount.stl, pcr-sherpa-mini-motor-holder.step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]
2021-08-21 E3D V6 & Orbiter 2.85mm Mod (#23)
    * Added Orbiter F2.85 Extruder mount for E3D V6 2.85mm Bowden Hotend
    * Added PTFE tube details to the description.
    * Typo fixed.
    * Added mount and Orbiter Image
    * More tweaks to description
    * Added photo
    * Get things in the right place.
    * Move stl to right place.
    [E3D-V6-Orbiter-2.85mm.stl, E3D-V6-Orbiter-2.85mm.stp]
2021-09-15 7530 Part Fan Remix
    [7530_part_fan_remix.step, 7530_part_fan_remix.stl]
2021-10-20 Added MabyCube EVA adaptors. (#26)
    * Added MabyCube EVA adaptors.
    * Added link to assembly instructions.
    [EVA_MC_top_bmg_mgn12.stl, EVA_MC_top_lgx_mgn12_a.stl, EVA_MC_top_mgn12.stl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]
2021-10-20 7530 Part Fan Remix (#30)
    [7530_part_fan_remix.step, 7530_part_fan_remix.stl]
2021-12-31 rasise brass mounted parts to EVA 2.4.1
    Rebuilt all brass insert parts from EVA 2.4.1
    also copied all brass-insert parts from Supersniffles into this repository to have all in one place
    added a new fanduct: Supersniffles monster horn duct remixed for Rapido UHF/Volcomosc/Volcano
    [Dragon-face-insert-1.2.stl, Dragon-support-insert-1.2.stl, Duct-2.1-straight-wide-high-inserts.stl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]
2021-12-31 fixed case of filename
    fixed case issue for filenames
    fixed formatting
    more case fixing
2022-01-01 Fix Mosquito support
    Fixed a faulty chamfer on the Mosquito support part
    Fixed heat insert size in description
    [mosquito_support-2.4.1-insert.stl, mosquito_support-2.4.1-r2-insert.stl]
2022-01-02 brass inserts: Updates
    Fixed Mosquito Mount
    Added Dual 5015 mod bottom with brass inserts, makes assembly easier
    [dual_5015_bottom_v3.stl, mosquito_support-2.4.1-r2-insert.stl]
2022-01-02 brass inserts: Raise fan ducts to 2.4.2
    [TriHorn Duct Default Narrow-2.4.2-inserts.stl, TriHorn Duct Default-2.4.2-inserts.stl, TriHorn Duct High Narrow-2.4.2-inserts.stl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]
2022-01-03 Fix filenames add dashes
    Update Mounts-brass-inserts.md
    fix filename
    fix filename
    Update mosquito_support-2.4.1-r2-insert.stl
    [TriHorn-Duct-Default-2.4.2-inserts.stl, TriHorn-Duct-Default-Narrow-2.4.2-inserts.stl, TriHorn-Duct-High-2.4.2-inserts.stl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]
2022-01-06 Update 7530_part_fan_remix.step
    STEP of the actual remix
    [7530_part_fan_remix.step]
2022-01-08 brass inserts: Corrected Dragon face
    There was a version issue with the Dragon face, uploaded the correct version as 2.4.2
    [dragon_face-2.4.1-inserts.stl, dragon_face-2.4.2-inserts.stl]
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2022-01-17 brass inserts: Add universal cable mount
    [unversal_cable_mount-2.4.2-inserts.stl]
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2022-01-22 brass inserts: Mosquito face improved
    [mosquito_face-2.4.1-insert.stl, mosquito_face-2.4.2-insert.stl]
